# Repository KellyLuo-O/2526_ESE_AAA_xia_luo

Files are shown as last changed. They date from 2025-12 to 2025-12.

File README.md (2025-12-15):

# 2526_ESE_AAA_xia_luo

## 6. Commande MCC basique

### 6.1. Génération de 4 PWM

- Fréquence de 20kHz :
   - f_clock = 170 MHz
   - on choisit PSC = 0 pour avoir le plus de résolution possible
   - comme on est en center align, la fréquence est divisé par 2 
   - on veut f = 20 kHz = f_pwm / 2 = f_clock / (2*ARR)
   - on choisit alors ARR = 4250 

- Temps mort minimum
  - Transistor du hacheur IRF540N :
    - rise time t_r : 44 ns
    - fall time t_f : 43 ns
    - turn off delay t_doff : 53 ns
    - turn on delay t_don : 11 ns
  - Si on somme on 151 ns
  - On utilise 200 ns pour plus de sécurité 
  - Pour avoir une temps mort de 200 ns :
     - On indique combien de fois on multiplie t_source = 1 / f_source = 1 / 170 MHz = 5.88 ns
     - Soit **34** * 5.88 ns = 200 ns
     - On indique dans l'ioc un deadtime de valeur **34**

- Résolution de 10 bits
   - On a ARR = 4250 > 1024
        
## 7. Commande en boucle ouverte, mesure de Vitesse et de courant

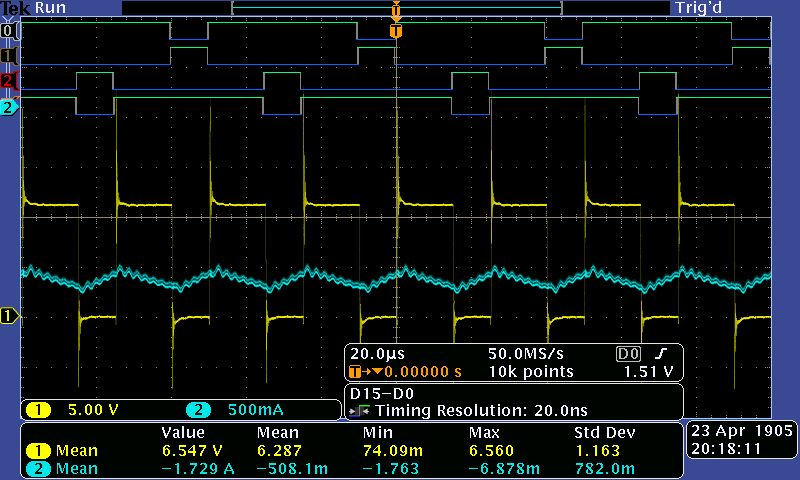
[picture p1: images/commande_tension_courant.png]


### 7.2. Mesure de courant

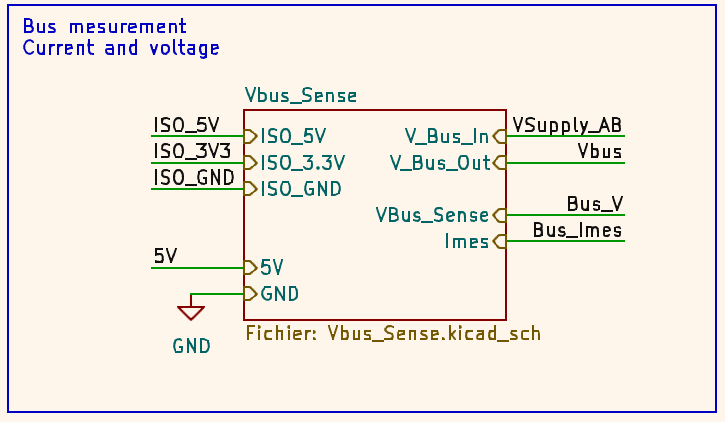
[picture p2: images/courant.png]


$$V_{out} = V_{ref} + G \cdot I_P$$

avec $$V_{ref}$$ = 1.65V.

G = 50mV/A.

$$I_P$$ le courant à mesurer.

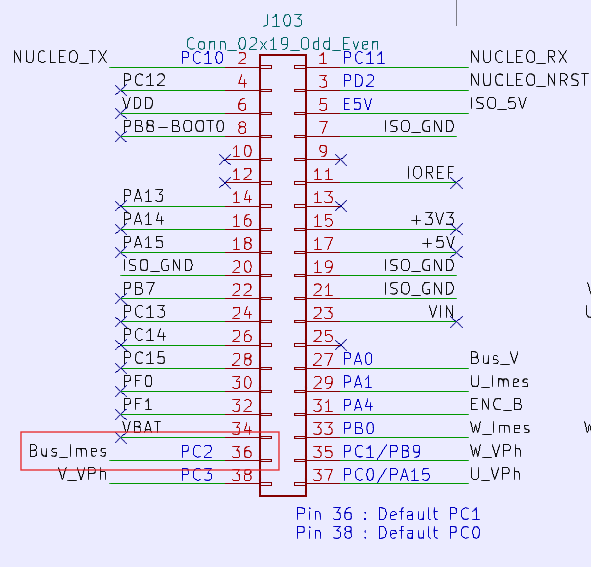
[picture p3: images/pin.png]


### 7.3. Mesure de vitesse

$$H(s) = \frac{\text{Mesure (tops/s)}}{\text{Vitesse (tr/min)}} = \frac{4 \cdot N_{PPR}}{60}$$

avec $N_{PPR}$ : Le nombre d'impulsions par tour de l'encodeur.

$4$ : Facteur de multiplication du STM32 (mode quadrature).

$60$ : Conversion minutes en secondes.

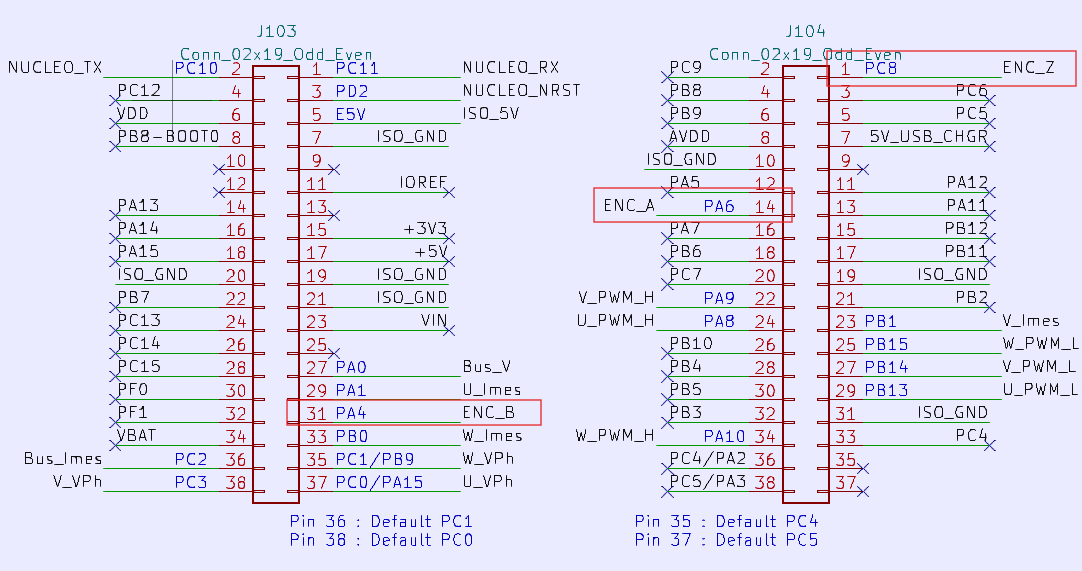
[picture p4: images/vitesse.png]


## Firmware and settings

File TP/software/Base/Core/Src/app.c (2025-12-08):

/*
 * app.c
 *
 *  Created on: Nov 11, 2025
 *      Author: nicolas
 */

#include "app.h"

#include "user_interface/shell.h"
#include "user_interface/led.h"
#include "motor_control/motor.h"
#include "acquisition/input_analog.h"

static char shell_uart2_received_char;

void init_device(void){
// Initialisation user interface
	// SHELL
	hshell1.drv.transmit = shell_uart2_transmit;
	hshell1.drv.receive = shell_uart2_receive;
	shell_init(&hshell1);
	HAL_UART_Receive_IT(&huart2, (uint8_t *)&shell_uart2_received_char, 1);

	// LED
	led_init();

	// BUTTON
//	button_init();
//
// Initialisation motor control
	// MOTOR
	motor_init();
	// ASSERV (PID)
//	asserv_init();
//
// Initialisation data acquistion
	// ANALOG INPUT
	input_analog_init();
	// ENCODER INPUT
//	input_encoder_init();
}

uint8_t shell_uart2_transmit(const char *pData, uint16_t size)
{
	HAL_UART_Transmit(&huart2, (uint8_t *)pData, size, HAL_MAX_DELAY);
	return size;
}

uint8_t shell_uart2_receive(char *pData, uint16_t size)
{
	*pData = shell_uart2_received_char;
	return 1;
}

void HAL_UART_RxCpltCallback(UART_HandleTypeDef *huart) {
	if (huart->Instance == USART2) {
		//		HAL_UART_Transmit(&huart2, (uint8_t *)&shell_uart2_received_char, 1, HAL_MAX_DELAY);
		HAL_UART_Receive_IT(&huart2, (uint8_t *)&shell_uart2_received_char, 1);
		shell_run(&hshell1);
	}
}

void loop(){

}

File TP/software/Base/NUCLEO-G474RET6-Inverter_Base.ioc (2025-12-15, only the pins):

Mcu.UserName=STM32G474RETx
PA0.GPIO_Label=Bus_V
PA0.Signal=ADC2_IN1
PA1.GPIO_Label=U_Imes
PA1.Signal=ADC1_IN2
PA10.GPIO_Label=W_PWM_H
PA10.Signal=S_TIM1_CH3
PA11.Signal=S_TIM1_CH4
PA12.Signal=GPIO_Output
PA13.GPIO_Label=T_SWDIO
PA13.Signal=SYS_JTMS-SWDIO
PA14.GPIO_Label=T_SWCLK
PA14.Signal=SYS_JTCK-SWCLK
PA2.Signal=USART2_TX
PA3.Signal=USART2_RX
PA4.Signal=S_TIM3_CH2
PA5.GPIO_Label=USR_LED
PA5.Signal=GPIO_Output
PA6.Signal=S_TIM3_CH1
PA8.GPIO_Label=U_PWM_H
PA8.Signal=S_TIM1_CH1
PA9.GPIO_Label=V_PWM_H
PA9.Signal=S_TIM1_CH2
PB0.Signal=ADC1_IN15
PB1.Signal=ADC1_IN12
PB13.GPIO_Label=U_PWM_L
PB13.Signal=TIM1_CH1N
PB14.GPIO_Label=V_PWM_L
PB14.Signal=TIM1_CH2N
PB15.GPIO_Label=W_PWM_L
PB15.Signal=TIM1_CH3N
PB3.GPIO_Label=T_SWO
PB3.Signal=SYS_JTDO-SWO
PC0.GPIO_Label=U_VPh
PC0.Signal=ADC2_IN6
PC1.GPIO_Label=W_VPh
PC1.Signal=ADC2_IN7
PC10.Signal=USART3_TX
PC11.Signal=USART3_RX
PC13.GPIO_Label=USR_BTN
PC13.Signal=GPXTI13
PC14-OSC32_IN.Signal=RCC_OSC32_IN
PC15-OSC32_OUT.Signal=RCC_OSC32_OUT
PC2.GPIO_Label=Bus_Imes
PC2.Signal=ADC1_IN8
PC3.GPIO_Label=V_VPh
PC3.Signal=ADC2_IN9
PC8.Signal=S_TIM3_CH3
PD2.GPIO_Label=NRST_SafetyUC
PD2.Signal=GPIO_Output
PF0-OSC_IN.Signal=RCC_OSC_IN
PF1-OSC_OUT.Signal=RCC_OSC_OUT

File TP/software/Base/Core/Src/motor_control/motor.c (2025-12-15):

/*
 * motor.c
 *
 *  Created on: Nov 11, 2025
 *      Author: nicolas
 */
#include <stdlib.h>
#include "tim.h"
#include "motor_control/motor.h"

#define PWM_ARR 4250-1

#define MOTOR_SPEED_MAX 3000

float dutyCycle = 0.0f;

void motor_init(void)
{

	__HAL_TIM_SET_AUTORELOAD(&htim1, PWM_ARR);

	__HAL_TIM_SET_COMPARE(&htim1, TIM_CHANNEL_1, (uint32_t)(dutyCycle * PWM_ARR));
	__HAL_TIM_SET_COMPARE(&htim1, TIM_CHANNEL_2, (uint32_t)((1 - dutyCycle) * PWM_ARR));


	shell_add(&hshell1, "speed", motor_speed, "Control motor speed (tr/min)");
	shell_add(&hshell1, "dutycycle", motor_dutycycle, "Control duty cycle (0-100)");
	shell_add(&hshell1, "motorStart", motor_start, "Start les PWM");
	shell_add(&hshell1, "motorStop", motor_stop, "Stop les PWM");
}


int motor_speed(h_shell_t* h_shell, int argc, char** argv)
{
	int size;
	int speedValue;

	if(argc!=2){
		size = snprintf(h_shell->print_buffer, SHELL_PRINT_BUFFER_SIZE, "Need 2 arguments : speed ###\r\n");
		h_shell->drv.transmit(h_shell->print_buffer, size);
		return HAL_ERROR;
	}

	// on vérifie que l'argument est bien un nombre
	char* str = argv[1];
	int reading_head = 0;
	while(str[reading_head] != '\0')
	{
		char c = str[reading_head];
		if(!(c >= '0' && c <= '9'))
		{
			size = snprintf(h_shell->print_buffer, SHELL_PRINT_BUFFER_SIZE, "2nd arguments isn't number\r\n");
			h_shell->drv.transmit(h_shell->print_buffer, size);
			return HAL_ERROR;
		}
		reading_head++;
	}

	speedValue = atoi(argv[1]);

	if(speedValue > MOTOR_SPEED_MAX){
		size = snprintf(h_shell->print_buffer, SHELL_PRINT_BUFFER_SIZE, "speed exceeding max value : 3000 tours/min\r\n");
		h_shell->drv.transmit(h_shell->print_buffer, size);
		return HAL_ERROR;
	}
	dutyCycle = (float)speedValue / (float)MOTOR_SPEED_MAX;
	__HAL_TIM_SET_COMPARE(&htim1, TIM_CHANNEL_1, (uint32_t)(dutyCycle * PWM_ARR));
	__HAL_TIM_SET_COMPARE(&htim1, TIM_CHANNEL_2, (uint32_t)((1 - dutyCycle) * PWM_ARR));

	size = snprintf(h_shell->print_buffer, SHELL_PRINT_BUFFER_SIZE, "Speed %d tr/min ==> DutyCycle %.2f\r\n", speedValue, dutyCycle);
	h_shell->drv.transmit(h_shell->print_buffer, size);
	return HAL_ERROR;
}


int motor_dutycycle(h_shell_t* h_shell, int argc, char** argv)
{
	int size;
	int value;

	if(argc!=2){
		size = snprintf(h_shell->print_buffer, SHELL_PRINT_BUFFER_SIZE, "Need 2 arguments : dutycycle ###\r\n");
		h_shell->drv.transmit(h_shell->print_buffer, size);
		return HAL_ERROR;
	}

	// on vérifie que l'argument est bien un nombre
	char* str = argv[1];
	int reading_head = 0;
	while(str[reading_head] != '\0')
	{
		char c = str[reading_head];
		if(!(c >= '0' && c <= '9'))
		{
			size = snprintf(h_shell->print_buffer, SHELL_PRINT_BUFFER_SIZE, "2nd arguments isn't number\r\n");
			h_shell->drv.transmit(h_shell->print_buffer, size);
			return HAL_ERROR;
		}
		reading_head++;
	}

	value = atoi(argv[1]);

	// on vérifie que l'argument est bien entre 0 et 100
	if(value > 100 || value < 0){
		size = snprintf(h_shell->print_buffer, SHELL_PRINT_BUFFER_SIZE, "duty cycle valeur de 0 à 100\r\n");
		h_shell->drv.transmit(h_shell->print_buffer, size);
		return HAL_ERROR;
	}

	//	float previous_dutyCycle = dutyCycle;
	//	for (int i=1; i<=3; i++)
	//	{
	//		float step = (((float)value/(float)100.0f) - previous_dutyCycle) / 3.0f;
	//		dutyCycle = previous_dutyCycle + step * (float)i;
	//
	//		__HAL_TIM_SET_COMPARE(&htim1, TIM_CHANNEL_1, (uint32_t)(dutyCycle * PWM_ARR));
	//		__HAL_TIM_SET_COMPARE(&htim1, TIM_CHANNEL_2, (uint32_t)((1 - dutyCycle) * PWM_ARR));
	//
	//		size = snprintf(h_shell->print_buffer, SHELL_PRINT_BUFFER_SIZE, "DutyCycle %.2f\r\n", dutyCycle);
	//		h_shell->drv.transmit(h_shell->print_buffer, size);
	//	}

	dutyCycle = (float)value/ (float)100.0f;
	__HAL_TIM_SET_COMPARE(&htim1, TIM_CHANNEL_1, (uint32_t)(dutyCycle * PWM_ARR));
	__HAL_TIM_SET_COMPARE(&htim1, TIM_CHANNEL_2, (uint32_t)((1 - dutyCycle) * PWM_ARR));

	size = snprintf(h_shell->print_buffer, SHELL_PRINT_BUFFER_SIZE, "DutyCycle %.2f\r\n", dutyCycle);
	h_shell->drv.transmit(h_shell->print_buffer, size);

	return HAL_OK;
}


int motor_start(h_shell_t* h_shell, int argc, char** argv)
{
	int size;

	if(argc != 1){
		size = snprintf(h_shell->print_buffer, SHELL_PRINT_BUFFER_SIZE, "usage : motorStart\r\n");
		h_shell->drv.transmit(h_shell->print_buffer, size);
		return HAL_ERROR;
	}

	dutyCycle = 0.50f;
	__HAL_TIM_SET_COMPARE(&htim1, TIM_CHANNEL_1, (uint32_t)(dutyCycle * PWM_ARR));
	__HAL_TIM_SET_COMPARE(&htim1, TIM_CHANNEL_2, (uint32_t)((1 - dutyCycle) * PWM_ARR));

	HAL_TIM_PWM_Start(&htim1, TIM_CHANNEL_1);
	HAL_TIM_PWM_Start(&htim1, TIM_CHANNEL_2);

	HAL_TIMEx_PWMN_Start(&htim1, TIM_CHANNEL_1);
	HAL_TIMEx_PWMN_Start(&htim1, TIM_CHANNEL_2);

	size = snprintf(h_shell->print_buffer, SHELL_PRINT_BUFFER_SIZE, "PWM started avec dutyCycle %.2f\r\n", dutyCycle);
	h_shell->drv.transmit(h_shell->print_buffer, size);
	return HAL_OK;
}


int motor_stop(h_shell_t* h_shell, int argc, char** argv)
{
	int size;

	if(argc != 1){
		size = snprintf(h_shell->print_buffer, SHELL_PRINT_BUFFER_SIZE, "usage : motorStop\r\n");
		h_shell->drv.transmit(h_shell->print_buffer, size);
		return HAL_ERROR;
	}

	HAL_TIM_PWM_Stop(&htim1, TIM_CHANNEL_1);
	HAL_TIM_PWM_Stop(&htim1, TIM_CHANNEL_2);
	HAL_TIMEx_PWMN_Stop(&htim1, TIM_CHANNEL_1);
	HAL_TIMEx_PWMN_Stop(&htim1, TIM_CHANNEL_2);
	return HAL_OK;
}

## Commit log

2025-12-01 Ajout des ressources de base
    [Arm_IRF540NBbF.kicad_sch, FAN.kicad_sch, Inverter_KiCAD.kicad_sch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]
2025-12-01 6.1. Génération de 4 PWM
2025-12-01 6.2. Commande de vitesse
2025-12-01 fix : counter mode
    [NUCLEO-G474RET6-Inverter_Base.ioc, motor.c]
2025-12-08 ajout des fonctions shell dutycycle pour controler directement le rapport cyclique et motorStart et motorStop
2025-12-08 readme update
    Added detailed section on basic MCC commands and PWM generation.
2025-12-08 deadtime 200 ns au lieu de 300ns
2025-12-08 motorStart qui met le rapport cycle à 0.5
    pas reussi à mettre la montée progressive de la vitesse
    parce que le hal_delay ne marche pas dans l'interruption (shell)
2025-12-08 Image des commandes, du courant et de la tension aux bornes du moteur
2025-12-08 acquisition adc polling du courant en valeur numérique
2025-12-15 7.2 Mesure de courant
2025-12-15 7. Commande en boucle ouverte, mesure de Vitesse et de courant
2025-12-15 Enhance README with detailed equations and parameters
    Clarify equations and parameters related to output voltage and speed measurement.
2025-12-15 mesure de courant
2025-12-15 les pin pour mesurer la vitesse
2025-12-15 Add KiCad backup files to .gitignore
